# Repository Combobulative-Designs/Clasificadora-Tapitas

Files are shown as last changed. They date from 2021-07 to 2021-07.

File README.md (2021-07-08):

# TAPINATOR 9KPP

Clasificadora de tapitas por color basada en Arduino desarrollada como proyecto
para la Universidad Católica del Uruguay. Este proyecto se realiza para la clase
de Taller Interdiciplinario de Introducción a la Ingenieria (TI3) en el 1er semestre
del 2021.

Aqui encontrara una descripcion del diseño final, incluyendo los componentes usados
y su ensamblaje para llegar a la unidad prototipo.

### Concepto

La clasificadora utiliza como cerebro a un Arduino UNO. Por medio de un sensor
de color, un micro servomotor, varios motores DC, y un motor paso a paso, este
realiza todo el proceso de clasificacion.

1. Las tapitas son introducidas en un contenedor en la parte superior.
2. Estas caen por una rampa con orificios con la medida justa para solo dejar pasar las tapitas que se pueden clasificar.
3. Las tapitas seleccionadas son revueltas por un motor DC hasta que caigan una por una en la posicion correcta por un pasaje.
4. Cada tapita cae en un disco operado por el motor paso a paso con 12 orificios.
5. El disco gira una posicion (1/12 de vuelta) en sentido horario, posicionando la tapita que cayo en frente al sensor de color.
6. En esta nueva posicion, el sensor lee el color de la tapita.
7. El servo motor gira para preparar el camino a seguir (en base del color) de la tapita procesada.
8. El disco gira una posicion mas, dejando a la tapita sobre un orificio por el cual esta cae.
9. La tapita cae y viaja por el camino seleccionado con el servomotor.
10. Como paso final, la tapita cae por el orificio del color leido, terminando en el recipiente apropiado.

### Materiales

Los materiales utilizados para la unidad prototipo final fueron placas de MDF cortadas
por laser, carton duro, y piezas de diseño 3D para impresion. Para el diseño y sus
medidas se especifico un grosor de 3mm para todas las placas y laminas.

### Piezas 3D

### Placas

### Componentes

Se utilizaron varios componentes electronicos obtenidos del kit inicial provisto por la Universidad,
mas otros adicionales obtenidos individualmente por el equipo. Entre estos se encuentran:

- Arduino UNO
- Protoboard/Breadboard
- Switch tactil x 4
- Resistencia de 10K Ohm x 4
- Resistencia de 200 Ohm x 3
- LED RGD x 1
- Sensor de color TCS34725 x 1
- Pantalla LCD de 1602 + Modulo I2C x 1
- Micro Servomotor SG90 x 1
- Motor Paso a Paso 28byj-48 + Driver ULN2003 x 1
- Relay de 5V con 1 canal x 1
- Motor DC de 3V x 4
- Placa de PCB x 1
- Switch de 2 posiciones x 1
- Modulo de reduccion CC-CC (Convertidor XL7015 V2 DC-DC)
- Transformador 220AC a 12V 2A x 1

Y muchos cablecitos.

### Circuito

El circuito utilizado fue el siguiente:

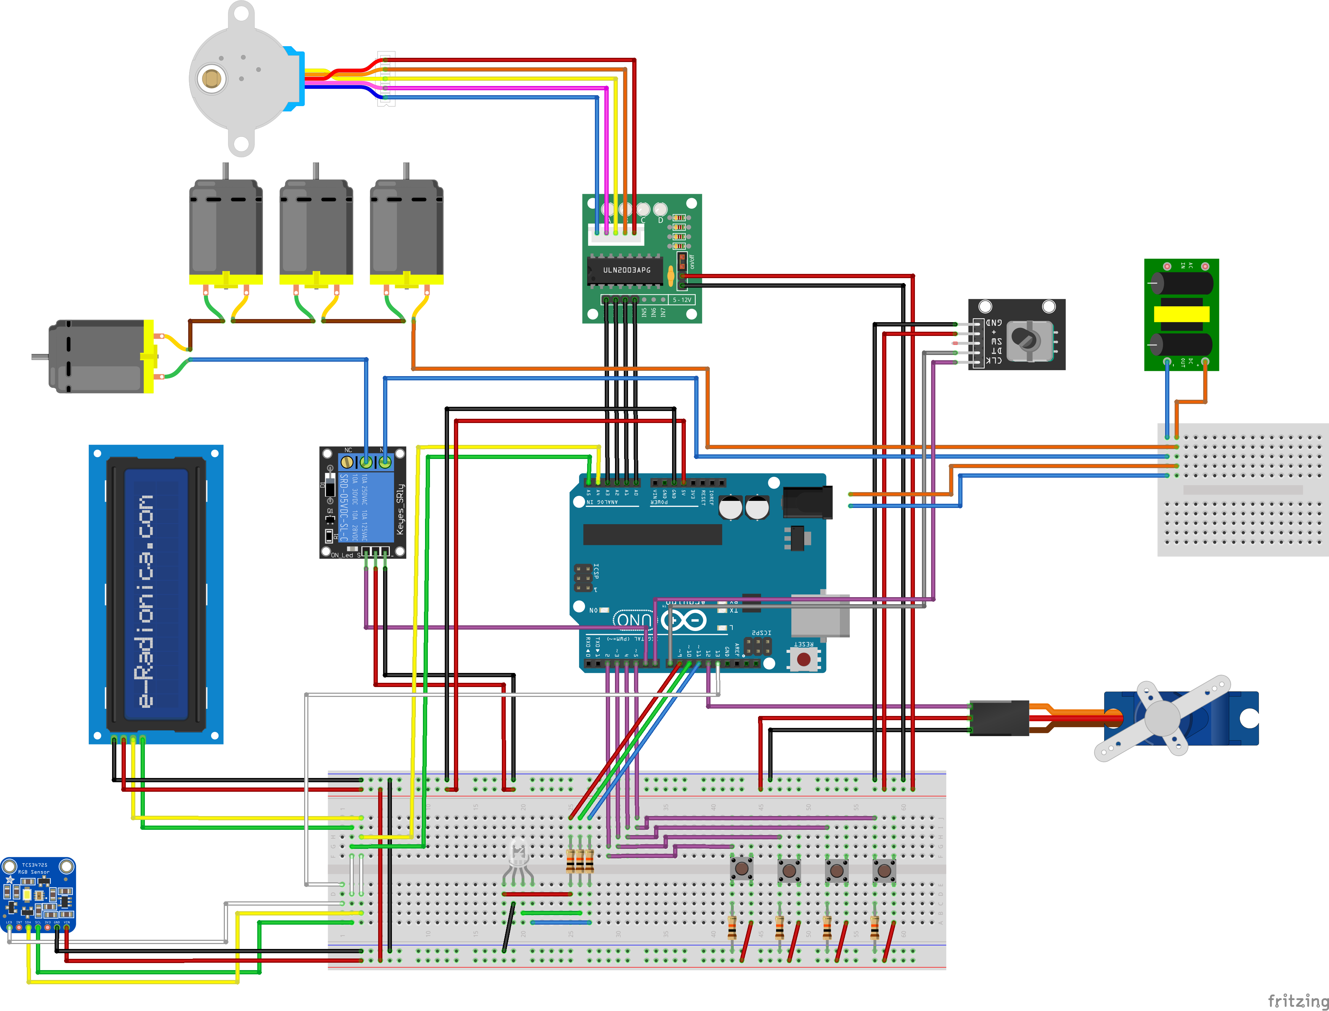
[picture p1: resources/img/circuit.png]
Diagrama


### Programacion del Arduino

Debido a haber varias funcionalidades necesarias para realizar el procedimiento
de clasificacion, se busco separar cada una y convertirla en una biblioteca a la 
cual referenciar luego desde el sketch principal.

Las librerias desarrolladas fueron:
- common_stuff (Funciones, enumerables, clases, y etc. en comun para todo el programa)
- sensor_control (control del sensor de color)
- stepper_control (control del motor paso a paso)
- servo_control (control del micro servo motor)
- rgb_control (control de LEDs RGB)
- simple_output_control (control de estado para pines de salida, usado para leds, reles, y buzzers)
- display_control (control del display LCD)
- menu_control (control del menu del programa)
- sorter_control (control del script de clasificacion automatica e interface entre el menu y los componentes)

El manejo por cada libreria de su componente asociado se realiza por un estado procesado en cada ciclo, 
y funciones que alteran este estado. Al llamar estas funciones, las variables que llevan el registro de 
cual es el estado actual son modifcadas. Luego, en el proximo ciclo y al procesar el estado del objeto,
este cambio es detectado y su componente se opera de acuerdo a este.

La operacion de todos los componentes, y los programas de accion atados a los items del menu, son manejados
por el objeto sorterControl. El objeto recive por referencia los objetos de la mayoria de los componentes
ya inicializados en el main.ino y opera sus metodos de acuerdo a distintos programas para realizar las 
tareas de clasificacion, configuracion, y etc. 

Estos programas son el centro de la clasificadora. Indican la tarea a realizar programada, y como operar
los componentes necesarios para llevarla a cabo, como puede ser el repetir los movimientos de stepper>sensor>servo
indefinidamente para la automatizacion completa.

La funcion loop principal del Arduino no interactua con la mayoria de los componentes, salvo para
pedirles que procesen sus estados respectivos. Solo interactua con los botones y el menu. Al detectarse
un cambio de estado de cada boton, el programa llama a al metodo relevante del menu para que este
procese la accion del usuario y que se debe hacer al respecto.

El menu es el que procesa estas acciones e interactua con los objetos displayControl (pantalla) y sorterControl 
(clasificadora) para navegar por el menu dentro de la pantalla, o iniciar un programa de la clasificadora. Por limitaciones
de la memoria dinamica del Arduino UNO, toda la estructura del menu fue guardada en la memoria del programa. De lo
contrario, el array con los datos ocuparia mas del 100% de la memoria por si solo.

Para la deteccion del color se considero un algoritmo el cual acepta los valores RGB detectados dentro de un rango de
0 a 255 como si fueran puntos en un espacio de tres dimenciones, y calcula la distancia euclideana entre este valor y
varios otros ya conocidos. Pero se termino utilizando otro cuyo resultado se aproxima a la distancia euclideana en un espacio
de colores L*u*v*. El concepto es el mismo pero dentro de otro espacio de colores. Un espacio el cual fue diseñado 
especificamente para la uniformidad perceptual.

### Librerias

<blockquote>
<details>
<summary markdown="span"><b>common_stuff.h</b></summary>

  Presenta funciones, enumeraciones, y estructuras de uso comun para todo el programa.
  * Funciones:
    * `char* ConvertColorCategoryToChar(ColorCategory)`: Convierte un dato ColorCategory a c-string.
    * `char* ConvertRGBColorToChar(RGBColor)`: Convierte un dato RGBColor a c-string.
  * Clases:
    *  `ButtonState()`: Maneja el estado de una boton asociado a un pin usando attach(int pin, int debounce_delay);
  * Enumeraciones:
    * `MenuUserActions`: Botones disponibles.
    * `RotationDirection`: A reloj o contra. Para el paso a paso.
    * `ButtonAction`: Estado de un boton.
    * `TextAlignment`: Justificacion para textos.
    * `SensorAuxLEDMode`: Modo de operacion del LED del sensor.
    * `RGBColors`: Colores para LEDs RGB.
    * `SorterActions`: Acciones individuales del sistema.
    * `SorterPrograms`: Programas de operacion que se pueden ejecutar.
    * `ColorCategories`: Categorias de colores a clasificar.
    * `MenuActions`: Acciones disponibles para el boton 'entrar' en el menu.
</details>
<details>
<summary><b>stepper_control.h</b></summary>
      
Definicion de clases asociadas al motor paso a paso.
* Clases:
  * `StepperControl(int, int, int, int)`: Controla e inicializa el motor.
    * `initialize()`: Inicializa el motor con maxima velocidad en 500 y posicion 0.
    * `processState()`: Opera el motor segun el estado del objecto.
    * `doCycling()`: Cambia el estado para realizar el ciclaje continuo del motor.
    * `doCapStep()`: Cambia el estado para realizar un giro de 30º.
    * `stopActions()`: Cambia el estado para detener todas las acciones.
    * `getCurrentAction()`: Devuelve la accion actual.
    * `isBusy()`: Devuelve verdadero si el estado actual es de descanzo.
* Enumeraciones:
  * `StepperActions`: Operaciones que puede realizar el motor paso a paso.
</details>
<details>
<summary><b>simple_output_control.h</b></summary>
      
Operacion de digital outputs.
* Clase:
  * `SOutputControl(int)`: Definicion, inicializacion, y operacion de digtal outputs.
    * `initialize()`: Inicializa la salida en el pin y lo configura.
    * `processState()`: Activa o desactiva el pin segun el estado dle objeto.
    * `on()`: Cambia el estado a HIGH.
    * `off()`: Cambia el estado a LOW.
</details>
<details>
<summary><b>servo_control.h</b></summary>

Operacion del servo motor.
* Clase:
  * `ServoControl(int)`: Operacion del servomotor, e inicializacion.
    * `initialize()`: Inicializacion del objeto servo.
    * `moveToColor(ColorCategory)`: A partir de color category, mover servo.
</details>
<details>
<summary><b>rgb_control.h</b></summary>
      
Activacion y manejo de LEDs RGB.
* Clase:
  * `RGBControl(int, int, int)`: 
    * `initialize()`: Configura valores por defecto.
    * `processState()`: Opera el LED segun el estado de este.
    * `setColor()` : Cambia el estado del LED.
    * `isRested()`: Devuelve verdadero si el led esta descansando.
</details>
<details>
<summary><b>display_control.h</b></summary>
 
Operacion de Displays LCD por I2C.
* Clases:
  * `TextLine()`: Guarda una linea del display y expone metodos para usarla.
    * `generateVisibleLine(int)`: Aplica alineacion y largo de cadena.
  * `DisplayControl(byte, int, int, int)`: Operacion del display LCD I2C.
    * `initialize()`: Inicializa el objeto display y crea chars especiales.
    * `processState()`: Opera el display de acuerdo a cambios de estado.
    * `setLineText(char [], int, enum TextAlignment)`: Cmabia el estado y conifugra una linea.
    * `navArrows()`: Mostrar flechas de navegacion en la linea inferior.
    * `noNavArrows()`: Ocultar flechas de navegacion en la linea inferior.
    * `rested()`: Devuelve verdadero si el display esta descansado.
</details>
<details>
<summary><b>sensor_control.h</b></summary>
 
Operacion del sensor RGB, y acceso a lecturas.
* Clases:
  * `SensorControl(int)`: Clase que inicializa y interactua con el sensor.
    * `initialize()`: Inicializa el objeto sensor y crea chars especiales.
    * `processState()`: Opera el sensor y LED segun el estado.
    * `setAuxLEDMode(SensorAuxLEDMode)`: Cambia el estado del LED.
    * `isBusy()`: Devuelve true si el sensor esta operando.
    * `getColorRead()`: Devuelva la ColorCategory asociada al color leido.
    * `getColorReadRGB()`: Devuelve un RGBColor con los datos leidos.
    * `requestColorReading()`: Cambia el estado del sensor para realizar una lectura.
</details>
<details>
<summary><b>sorter_control.h</b></summary>
 
Ejecucion de Programas de automatizacion, rastreo de estadistica, y interfaz con otras librerias.
* Clases:
  * `SorterControl(SensorControl (&), StepperControl (&), ServoControl (&), SOutputControl (&), RGBControl (&), DisplayControl (&))`: Clase que hace de interfaz entre el menu y los componentes, y ejecuta programas.
    * `initialize()`: Llama al inicializador de todos los objetos para componentes.
    * `processState()`: Ejecuta pogramas segun el estado.
    * `startProgram()`: Inicia un programa de ejecucion.
    * `stopProgram()`: Levanta el flag que los programas no bloqueantes toman para parar.
    * `isBusy()`: Devuelve true si se esta ejecutanto algun programa.
</details>
<details>
<summary><b>menu_control.h</b></summary>
 
Presenta un menu por display al usuario y le permite interactuar con la clasificadora por medio de una botonera.
* Clases:
  * `MenuControl(const MenuItemS (&)[38], DisplayControl (&), SorterControl (&))`: Maneja interacciones entre clasificadora e usuario por botonera y display
    * `initialize()`: Inicializa el objeto SorterControl.
    * `processState()`: Dependiendo de la accion activa, navega el menu o actuva programas del SorterControl.
    * `triggerUserAction(MenuUserActions)`: Cambia el estado configurando la accion activa por la recivida.
    * `getCurrentAction()`: Devuelve la accion activa.
    * `getCurrentMenuItemId()`: Devuelve el id del item de menu actual.
    * `getMenuItem()`: Devuelve el item de menu para dado id.
    * `getNextSiblingId()`: Devuelve el id del item de menu hermano siguiente desde el item de menu actual.
    * `getPrevSiblingId()`: Devuelve el id del item de menu hermano anterior desde el item de menu actual.
    * `getSiblingCount()`: Devuelve la cantidad de hermanos para el item de menu actual.
    * `getFirstChild()`: Devuelve el id del item de menu con indice 0 dentro de los hijos del item de menu actual.
    * `inactive()`: Devuelve verdadero si el menu se encuentra inactivo.
    * `canGoBack()`: Devuelve verdadero si existe abuelo del item del menu actual.
</details>
</blockquote>

Adicionalmente se utilizaron las librerias de 3er siguientes:
- AccelStepper
- LiquidCrystal_I2C
- PROGMEM_readAnything
- Servo
- Arduino

Por ultimo, la Universidad nos provio de las siguientes librerias para operar el sensor de color:
- COLOR
- Adafruit_TCS34725
- ColorConverterLib.h

### Ensamblado

### Operacion

### Fuentes usadas

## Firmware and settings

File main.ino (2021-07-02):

#include <Servo.h>
#include <AccelStepper.h>

#include "common_stuff.h"

#include "sensor_dummy.h"
//#include "servo_control.h"
//#include "stepper_control.h"
//#include "encoder_control.h"
#include "display_control.h"
#include "menu_control.h"

#define PIN_BUTTON_PREV 2
#define PIN_BUTTON_NEXT 3
#define PIN_BUTTON_RETURN 4
#define PIN_BUTTON_ENTER 5

#define PIN_ENCODER_CLK 6
#define PIN_ENCODER_DT 7

#define PIN_STEPPER_IN1 8
#define PIN_STEPPER_IN2 9
#define PIN_STEPPER_IN3 10
#define PIN_STEPPER_IN4 11

#define PIN_SERVO_SIGNAL 12

#define PIN_SENSOR_LED 13

#define CYCLE_DURATION 20
#define DEBOUNCE_DELAY 50
#define REST_DELAY 50

enum ColorCategory categoryDetected = ColorCategory::Blacks;

const MenuItemS PROGMEM menu_01 = {1, 0, 0, "TAPITANATOR 9KPP\0\0\0", 17};
const MenuItemS PROGMEM menu_02 = {2, 1, 0, "Iniciar Ya\0\0\0\0\0\0\0\0\0", 0};
const MenuItemS PROGMEM menu_03 = {3, 1, 1, "Clasificar\0\0\0\0\0\0\0\0\0", 16};
const MenuItemS PROGMEM menu_04 = {4, 1, 2, "Configurar\0\0\0\0\0\0\0\0\0", 16};
const MenuItemS PROGMEM menu_05 = {5, 1, 3, "Estadistica\0\0\0\0\0\0\0\0", 16};
const MenuItemS PROGMEM menu_06 = {6, 3, 0, "Automatico\0\0\0\0\0\0\0\0\0", 16};
const MenuItemS PROGMEM menu_07 = {7, 6, 0, "Comenzar\0\0\0\0\0\0\0\0\0\0\0", 0};
const MenuItemS PROGMEM menu_08 = {8, 4, 0, "Calib. disco\0\0\0\0\0\0\0", 16};
const MenuItemS PROGMEM menu_09 = {9, 8, 0, "A reloj\0\0\0\0\0\0\0\0\0\0\0\0", 5};
const MenuItemS PROGMEM menu_10 = {10, 8, 1, "Contra reloj\0\0\0\0\0\0\0", 6};
const MenuItemS PROGMEM menu_11 = {11, 4, 0, "Acerca de\0\0\0\0\0\0\0\0\0\0", 16};
const MenuItemS PROGMEM menu_12 = {12, 11, 0, "Equipo\0\0\0\0\0\0\0\0\0\0\0\0\0", 16};
const MenuItemS PROGMEM menu_13 = {13, 12, 0, "Vogel J.\0\0\0\0\0\0\0\0\0\0\0", 17};
const MenuItemS PROGMEM menu_14 = {14, 12, 1, "Ponce.. E.\0\0\0\0\0\0\0\0\0", 17};
const MenuItemS PROGMEM menu_15 = {15, 12, 2, "Jorajuria S.\0\0\0\0\0\0\0", 17};
const MenuItemS PROGMEM menu_16 = {16, 12, 3, "Jauregui R.\0\0\0\0\0\0\0\0", 17};
const MenuItemS PROGMEM menu_17 = {17, 11, 1, "Clase\0\0\0\0\0\0\0\0\0\0\0\0\0\0", 16};
const MenuItemS PROGMEM menu_18 = {18, 17, 0, "U. Catolica\0\0\0\0\0\0\0\0", 17};
const MenuItemS PROGMEM menu_19 = {19, 17, 1, "2021 Sem 1\0\0\0\0\0\0\0\0\0", 17};
const MenuItemS PROGMEM menu_20 = {20, 17, 2, "TI3 Grupo B\0\0\0\0\0\0\0\0", 17};
const MenuItemS PROGMEM menu_21 = {21, 17, 3, "Equipo 12\0\0\0\0\0\0\0\0\0\0", 17};
const MenuItemS PROGMEM menu_22 = {22, 3, 1, "Manual\0\0\0\0\0\0\0\0\0\0\0\0\0", 16};
const MenuItemS PROGMEM menu_23 = {23, 22, 0, "Mover disco\0\0\0\0\0\0\0\0", 4};
const MenuItemS PROGMEM menu_24 = {24, 22, 1, "Leer color\0\0\0\0\0\0\0\0\0", 2};
const MenuItemS PROGMEM menu_25 = {25, 22, 2, "Mover sensor\0\0\0\0\0\0\0", 3};
const MenuItemS PROGMEM menu_26 = {26, 3, 2, "Paso a paso\0\0\0\0\0\0\0\0", 16};
const MenuItemS PROGMEM menu_27 = {27, 26, 0, "Siguiente\0\0\0\0\0\0\0\0\0\0", 1};
const MenuItemS PROGMEM menu_28 = {28, 5, 0, "Tiempo\0\0\0\0\0\0\0\0\0\0\0\0\0", 7};
const MenuItemS PROGMEM menu_29 = {29, 5, 1, "Cantidades\0\0\0\0\0\0\0\0\0", 16};
const MenuItemS PROGMEM menu_30 = {30, 29, 0, "Rojos\0\0\0\0\0\0\0\0\0\0\0\0\0\0", 9};
const MenuItemS PROGMEM menu_31 = {31, 29, 1, "Azules\0\0\0\0\0\0\0\0\0\0\0\0\0", 10};
const MenuItemS PROGMEM menu_32 = {32, 29, 2, "Verdes\0\0\0\0\0\0\0\0\0\0\0\0\0", 11};
const MenuItemS PROGMEM menu_33 = {33, 29, 3, "Amarillos\0\0\0\0\0\0\0\0\0\0", 12};
const MenuItemS PROGMEM menu_34 = {34, 29, 4, "Blancos\0\0\0\0\0\0\0\0\0\0\0\0", 14};
const MenuItemS PROGMEM menu_35 = {35, 29, 5, "Grises\0\0\0\0\0\0\0\0\0\0\0\0\0", 15};
const MenuItemS PROGMEM menu_36 = {36, 29, 6, "Negros\0\0\0\0\0\0\0\0\0\0\0\0\0", 13};

const MenuItemS menu[36] PROGMEM = {
  menu_01, menu_02, menu_03, menu_04, menu_05, menu_06, menu_07, menu_08, menu_09, menu_10,
  menu_11, menu_12, menu_13, menu_14, menu_15, menu_16, menu_17, menu_18, menu_19, menu_20,
  menu_21, menu_22, menu_23, menu_24, menu_25, menu_26, menu_27, menu_28, menu_29, menu_30,
  menu_31, menu_32, menu_33, menu_34, menu_35, menu_36
};

const MenuItem menu2[36];

ButtonState buttonPrev;
ButtonState buttonNext;
ButtonState buttonReturn;
ButtonState buttonEnter;

//RotaryEncoderControl encoderControl;
//StepperControl stepperControl(PIN_STEPPER_IN1, PIN_STEPPER_IN2, PIN_STEPPER_IN3, PIN_STEPPER_IN4);
//ServoControl servoControl(PIN_SERVO_SIGNAL);
DisplayControl displayControl(0x27, 16, 2, REST_DELAY);
MenuControl menuControl(menu2, displayControl);


void setup() {
    Serial.begin(9600);

    buttonPrev.attach(PIN_BUTTON_PREV, DEBOUNCE_DELAY);
    buttonNext.attach(PIN_BUTTON_NEXT, DEBOUNCE_DELAY);
    buttonReturn.attach(PIN_BUTTON_RETURN, DEBOUNCE_DELAY);
    buttonEnter.attach(PIN_BUTTON_ENTER, DEBOUNCE_DELAY);

    //InitSensor();
    displayControl.initialize();
    //stepperControl.initialize();
    //servoControl.initialize();
    /*encoderControl.attach(PIN_ENCODER_CLK,
                          PIN_ENCODER_DT);*/

    pinMode(PIN_SENSOR_LED, OUTPUT);
    digitalWrite(PIN_SENSOR_LED, HIGH);

    displayControl.noNavArrows();
    displayControl.setLineText(
            (char*)"TAPITANATOR 9KPP",
            0,
            TextAlignment::Center);
    displayControl.setLineText(
            (char*)"¡Bienvenido!",
            1,
            TextAlignment::Center);

    delay(5000);

    menuControl.initialize();
}

void loop() {
    buttonPrev.processState();
    buttonNext.processState();
    buttonReturn.processState();
    buttonEnter.processState();

    if (buttonPrev.getUserAction() == ButtonAction::Release) menuControl.triggerUserAction(MenuUserActions::Next);
    if (buttonNext.getUserAction() == ButtonAction::Release) menuControl.triggerUserAction(MenuUserActions::Next);
    if (buttonReturn.getUserAction() == ButtonAction::Release) menuControl.triggerUserAction(MenuUserActions::Next);
    if (buttonEnter.getUserAction() == ButtonAction::Release) menuControl.triggerUserAction(MenuUserActions::Next);

    menuControl.processState();
    displayControl.processState();
}

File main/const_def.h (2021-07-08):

#ifndef GITHUB_REPO_PIN_DEFINITIONS_H
#define GITHUB_REPO_PIN_DEFINITIONS_H

#define PIN_BUTTON_PREV 2
#define PIN_BUTTON_NEXT 3
#define PIN_BUTTON_RETURN 4
#define PIN_BUTTON_ENTER 5

#define PIN_RELAY_SIGNAL 6

#define PIN_ENCODER_CLK 7
#define PIN_ENCODER_DT 8

#define PIN_RGB_LED_RED 9
#define PIN_RGB_LED_GRE 10
#define PIN_RGB_LED_BLU 11

#define PIN_SERVO_SIGNAL 12

#define PIN_SENSOR_AUX_LED 13

#define PIN_STEPPER_IN1 17
#define PIN_STEPPER_IN2 16
#define PIN_STEPPER_IN3 15
#define PIN_STEPPER_IN4 14

#define DISPLAY_ADDRESS 0x27
#define DISPLAY_ROWS 2
#define DISPLAY_COLUMNS 16

#define DEBOUNCE_DELAY 50
#define REST_DELAY 50

#endif //GITHUB_REPO_PIN_DEFINITIONS_H

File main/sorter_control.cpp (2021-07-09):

#include <Arduino.h>

#include "sorter_control.h"

#include "common_stuff.h"
#include "sensor_control.h"
#include "servo_control.h"
#include "stepper_control.h"
#include "rgb_control.h"
#include "display_control.h"
#include "progmem_data.h"
#include "PROGMEM_readAnything.h"


SorterControl::SorterControl(SensorControl &p_sensorControl,
                             StepperControl &p_stepperControl,
                             ServoControl &p_servoControl,
                             SOutputControl &p_sOutputControl,
                             RGBControl &p_rgbControl,
                             DisplayControl &p_displayControl
                             ) :
                             sensorControl(p_sensorControl),
                             stepperControl(p_stepperControl),
                             servoControl(p_servoControl),
                             sOutputControl(p_sOutputControl),
                             rgbControl(p_rgbControl),
                             displayControl(p_displayControl),
                             initialized(false),
                             locked(false),
                             stopSignal(false),
                             lastAction(SorterActions::ServoTurn),
                             currentProgram(SorterPrograms::Startup),
                             currentProgramStep(1),
                             programStartTime(0),
                             colorCategoryRead(ColorCategory::Blacks),
                             lastRGBReading{0,0,0},
                             rgbSamplesForAvg{0},
                             processedTotal(0),
                             processedByColor{0,0,0,0,0,0,0},
                             avgIndex(0),
                             activeSampleArchive(0)
                             {}

void SorterControl::initialize() {
    if (!initialized) {
        sensorControl.initialize();
        stepperControl.initialize();
        servoControl.initialize();
        sOutputControl.initialize();
        rgbControl.initialize();
        displayControl.initialize();

        initialized = true;
    }
}

void SorterControl::startProgram(enum SorterPrograms p_program) {
    if (initialized and currentProgram == SorterPrograms::Rest) {
        currentProgram = p_program;
        currentProgramStep = 1;
    }
}

void SorterControl::stopProgram() {
    if (initialized and currentProgram != SorterPrograms::Rest and !locked) {
        stopSignal = true;
        displayControl.noNavArrows();
        displayControl.setLineText((char*)"Deteniendo\0\0\0\0\0\0\0\0\0", 0, TextAlignment::Center);
        displayControl.setLineText((char*)"...\0\0\0\0\0\0\0\0\0\0\0\0\0\0\0\0", 1, TextAlignment::Center);
    }
}

bool SorterControl::isBusy() {
    if (initialized) {
        if (currentProgram == SorterPrograms::Rest) {
            return false;
        } else {
            return true;
        }
    } else {
        return false;
    }
}

void SorterControl::processState() {
    if (initialized) {
        switch (currentProgram) {
            case SorterPrograms::Rest:
                break;
            case SorterPrograms::ManualStepper:
                PGM_ManualStepper();
                break;
            case SorterPrograms::ManualServo:
                PGM_ManualServo();
                break;
            case SorterPrograms::ManualSensor:
                PGM_ManualSensor();
                break;
            case SorterPrograms::ByStepNext:
                PGM_ByStepNext();
                break;
            case SorterPrograms::Automatic:
                PGM_Automatic();
                break;
            case SorterPrograms::CycleStepper:
                //PGM_SensorData();
                PGM_CycleStepper();
                break;
            case SorterPrograms::CalibrateSensor:
                PGM_SensorAvg();
                break;
            case SorterPrograms::Startup:
                PGM_Startup();
                break;
            default:
                break;
        }
    }
}

void SorterControl::PGM_ManualStepper() {
    if (initialized) {
        switch (currentProgramStep) {
            case 1:
                locked = true;
                programStartTime = millis();
                currentProgramStep++;
                break;
            case 2:
                displayControl.noNavArrows();
                displayControl.setLineText((char*)"Mov. disco\0\0\0\0\0\0\0\0\0", 0, TextAlignment::Center);
                displayControl.setLineText((char*)"...\0\0\0\0\0\0\0\0\0\0\0\0\0\0\0\0", 1, TextAlignment::Center);
                currentProgramStep++;
                break;
            case 3:
                if (!stepperControl.isBusy()) {
                    stepperControl.doCapStep();
                    currentProgramStep++;
                }
                break;
            case 4:
                if (millis() - programStartTime >= 1000) currentProgramStep++;
                break;
            case 5:
                locked = false;
                currentProgramStep = 99;
                currentProgram = SorterPrograms::Rest;
                lastAction = SorterActions::ServoTurn;
                break;
            default:
                break;
        }
    }
}

void SorterControl::PGM_ManualServo() {
    if (initialized) {
        switch (currentProgramStep) {
            case 1:
                locked = true;
                programStartTime = millis();
                currentProgramStep++;
                break;
            case 2:
                displayControl.noNavArrows();
                displayControl.setLineText((char*)"Mov. servo\0\0\0\0\0\0\0\0\0", 0, TextAlignment::Center);
                displayControl.setLineText((char*)"...\0\0\0\0\0\0\0\0\0\0\0\0\0\0\0\0", 1, TextAlignment::Center);
                currentProgramStep++;
                break;
            case 3:
                servoControl.moveToColor(colorCategoryRead);
                rgbControl.setColor(RGBColors::Green);
                currentProgramStep++;
                break;
            case 4:
                if (millis() - programStartTime >= 1000) currentProgramStep++;
                break;
            case 5:
                locked = false;
                rgbControl.setColor(RGBColors::Off);
                currentProgramStep = 99;
                currentProgram = SorterPrograms::Rest;
                lastAction = SorterActions::ServoTurn;
                break;
            default:
                break;
        }
    }
}
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

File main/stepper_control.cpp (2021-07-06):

#include <AccelStepper.h>

#include <Arduino.h>

#include "common_stuff.h"

#include "stepper_control.h"

StepperControl::StepperControl(int p_pinIN1, int p_pinIN2, int p_pinIN3, int p_pinIN4) :
    initialized(false),
    positionCounter(0),
    nextPosition(0),
    actionChange(false),
    currentAction(StepperActions::Resting),
    previousAction(StepperActions::Resting),
    stepSize(512),
    stepMax(4096),
    stepper(8, p_pinIN1, p_pinIN3, p_pinIN2, p_pinIN4)
    {}

StepperActions StepperControl::getCurrentAction() {return currentAction;}

void StepperControl::initialize() {
    if (!initialized) {
        stepper.setCurrentPosition(0);
        stepper.setMaxSpeed(500);

        initialized = true;
    }
}

void StepperControl::processState() {
    if (initialized) {
        if (stepper.currentPosition() >= stepMax) stepper.setCurrentPosition(stepper.currentPosition() - stepMax);
      
        switch (currentAction) {
            case StepperActions::Resting:
                if (actionChange) {
                    actionChange = false;
                }
                break;
            case StepperActions::CapStep:
                if (actionChange) {
                    actionChange = false;
                    nextPosition = positionCounter + stepSize;
                    if (nextPosition >= stepMax) { nextPosition = nextPosition - stepMax; }
                    stepper.enableOutputs();
                    stepper.setSpeed(500);
                    stepper.moveTo(nextPosition);
                }
                if (stepper.currentPosition() == stepper.targetPosition()) {
                    positionCounter = nextPosition;
                    actionChange = true;
                    currentAction = StepperActions::Stopping;
                } else {
                    stepper.setSpeed(500);
                    stepper.runSpeed();
                }
                break;
            case StepperActions::Cycling:
                if (actionChange) {
                    actionChange = false;
                    nextPosition = positionCounter + stepSize;
                    if (nextPosition >= stepMax) { nextPosition = nextPosition - stepMax; }
                    stepper.enableOutputs();
                    stepper.setSpeed(100);
                    stepper.moveTo(nextPosition);
                }
                if (stepper.currentPosition() == stepper.targetPosition()) {
                    positionCounter = nextPosition;
                    nextPosition = positionCounter + stepSize;
                    if (nextPosition >= stepMax) { nextPosition = nextPosition - stepMax; }
                    stepper.moveTo(nextPosition);
                    stepper.setSpeed(100);
                    stepper.runSpeed();
                } else {
                    stepper.setSpeed(100);
                    stepper.runSpeed();
                }
                break;
            case StepperActions::Stopping:
                if (actionChange) {
                    actionChange = false;
                    stepper.disableOutputs();
                    if (previousAction == StepperActions::Cycling) {
                        stepper.setCurrentPosition(0);
                        positionCounter = 0;
                    }
                    actionChange = true;
                    currentAction = StepperActions::Resting;
                }
                break;
        }

        previousAction = currentAction;
    }
}

void StepperControl::doCycling() {
    if (initialized) {
        if (currentAction == StepperActions::Resting) {
            actionChange = true;
            currentAction = StepperActions::Cycling;
        }
    }
}

void StepperControl::doCapStep() {
    if (initialized) {
        if (currentAction == StepperActions::Resting) {
            actionChange = true;
            currentAction = StepperActions::CapStep;
        }
    }
}
void StepperControl::stopActions() {
    if (initialized) {
        if (currentAction == StepperActions::CapStep || currentAction == StepperActions::Cycling) {
            actionChange = true;
            currentAction = StepperActions::Stopping;
        }
    }
}

bool StepperControl::isBusy() {
    if (initialized) {
        if (currentAction == StepperActions::Resting) {
            return false;
        } else {
            return true;
        }
    } else {
        return false;
    }
}

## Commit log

2021-06-29 Changes after testing. StepperControl needs rewriting.
2021-06-30 Stepper, servo, and sensor working. Next is the display.
2021-07-02 First menu literal string length corrected.
    [main.ino]
2021-07-02 Removed unused class, and serial.prints.
2021-07-02 Circuit and removing commented sections.
    [circuit.fzz]
2021-07-03 Updated circuit diagram.
    [circuit.fzz]
2021-07-03 Remade sensor library for menu/automatation integration.
2021-07-04 RGB control library for operating RGB LEDs.
2021-07-06 Relay control in da house.
2021-07-07 Renamed RelayControl to account for other outputs. Now it's SimpleOutputControl.
2021-07-07 Updating SensorControl for using color distance against samples for readings.
2021-07-07 Testing sensor control functions.
2021-07-08 Work with functions for sensor training.
2021-07-08 Work on traning the sensor v2.
